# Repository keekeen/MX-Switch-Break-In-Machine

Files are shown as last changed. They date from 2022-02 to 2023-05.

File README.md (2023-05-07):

# MX Switch Break-In Machine
A simple machine designed to actuate/ break-in MX style switches consistently and repetitively for a smoother push feel. Watch the [assembly process and operation](https://www.youtube.com/watch?v=iYIlCdo38ZM&list=PLLd9RKaLkD3lO_kQBJ3w394Xko4Nm3RR9) of the machine here.

Also do check out my latest design and endeavour here: https://geekhack.org/index.php?topic=120229.msg3160750#msg3160750 🙆🏻‍♂️

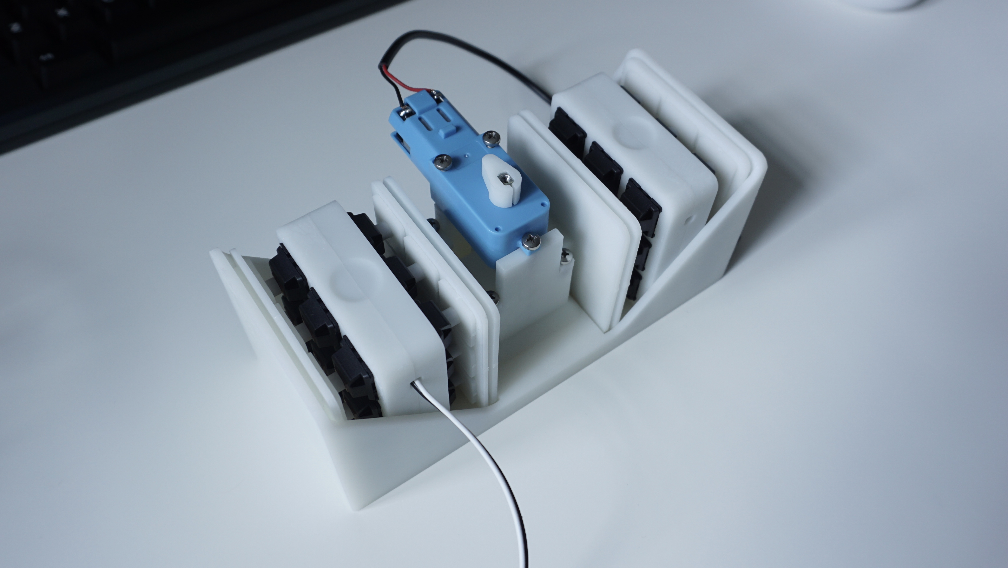
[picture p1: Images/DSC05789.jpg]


[snapshot]: /Images/DSC05789.jpg "Machine Snapshot"

## Specifications
- Max number of switches: 36
- Compatibility: 
  -  MX style switches with total travel distance of 4mm
  -  MX style switches with total travel distance less than 4mm (tweaks required for this)

## Notes ⚠️
- The provided files are to be used at your own risk.
- The dimensional tolerances may vary between 3D printers. See acceptable tolerances under [`Production/Technical-Drawings`](/Production/Technical-Drawings).
- The complete units showed in pictures and videos shared in this repo were printed with [JLCPCB 3D printing service](https://cart.jlcpcb.com/quote), with material of 8000 Resin, and remarked to print at an 30/45 angle for better Z-axis accuracy.
- Do ensure to run the machine at a ventilated area or fan-cooled to prevent the motor from overheating.

## Bill of materials (BOM) 📜
The following is the number of quantities required for each part to assemble a complete unit. The part files required to print are under the [`Production`](/Production) folder.

Parts required to print:
| Part | Qty | Comment |
| --- | --- | --- |
| Actuation Plate | 2 | - |
| Off Center Actuation Plate | 4 | - |
| Switch Holder | 4 | - |
| Flat Profile Keycap *or 10xFlat Profile Keycap* | 36 *or 4*  | - |
| Machine Housing | 1 | - |
| Machine Housing 1 *or 4xMachine Housing 1* | 2 *or 1* | - |
| Motor-Adjuster | 1 | - |
| Scotch Yoke | 1 | - |

Parts required to purchase:
| Part | Qty | Comment | References |
| --- | --- | --- | --- |
| TT 1:90 Gearbox DC Motor | 1 | Measured about 155 actutations/min, 5.4 hours for 50k actuations (measurement based on my purchased motor) | [link 1](https://shopee.sg/Large-Price-Metal-Gear-Robot-Smart-Car-Reduce-Speed-Motor-Tt-Motor-i.191993938.3917622642) |
| *or TT 1:48 Gearbox DC Motor* | 1 | Motor runs hot over long run, measured about 400 actutations/min, 2.1 hours for 50k actuations (measurement based on my purchased motor) | [link 2](https://www.adafruit.com/product/3777) |
| HK 0306 Needle Roller Bearing | 2 | - | [link 1](https://www.skf.com/us/products/rolling-bearings/roller-bearings/needle-roller-bearings/drawn-cup-needle-roller-bearings/productid-HK%200306%20TN) |
| M3 x 8mm Screw | 6 | - | - |
| M3 x 12mm Screw | 2 | - | - |
| M3 x 25mm Screw | 2 | - | - |
| Female USB C to 2-pin 22 AWG Wires | 1 | - | [link 1](https://www.aliexpress.com/item/1005001388133794.html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) <br> [link 2](https://www.aliexpress.com/item/1005002271810476.html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) |
| 8mm Diameter Bumpons | 4 | Optional | [link 1](https://shopee.sg/MAGIC-100PCS-Sheet-Soft-Buffer-Sticker-Furniture-Accessories-Gel-Shock-Absorber-Rubber-Silicone-Pads-Cabinets-Door-Stop-Anti-collision-Toilets-Bump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) |

## To-Do 📝
- A guide on breaking-in switches that have shorter travel distance will be shared soon.

## Changelog 📒
- `05/02/2022:` Initial part files commit 

## Reach me at 📩
- Discord: https://discordapp.com/users/keekeen#1351
  - Feel free to send me your enquires if you have doubt reproducing a unit for yourself.

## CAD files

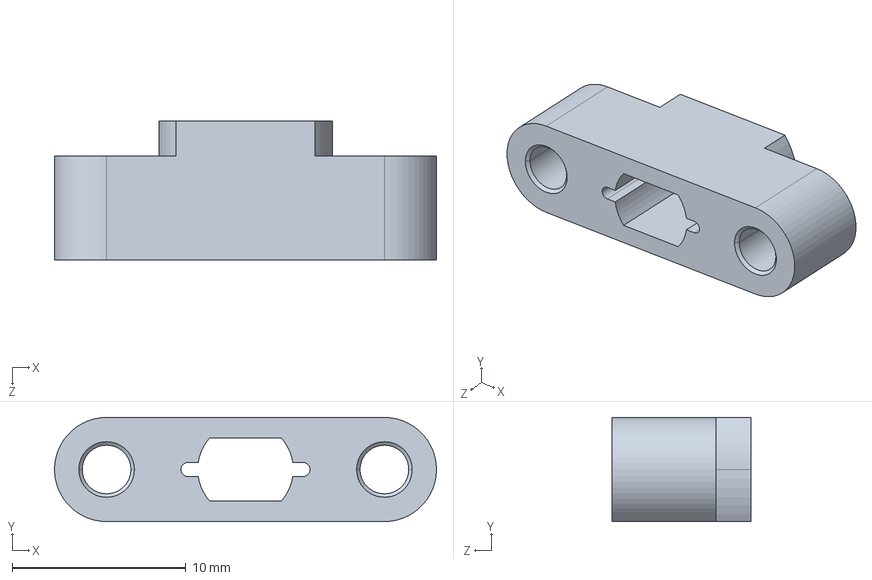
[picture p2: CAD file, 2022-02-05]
Production/STEP/Scotch-Yoke.STEP
22.0 x 6.00 x 8.00 mm

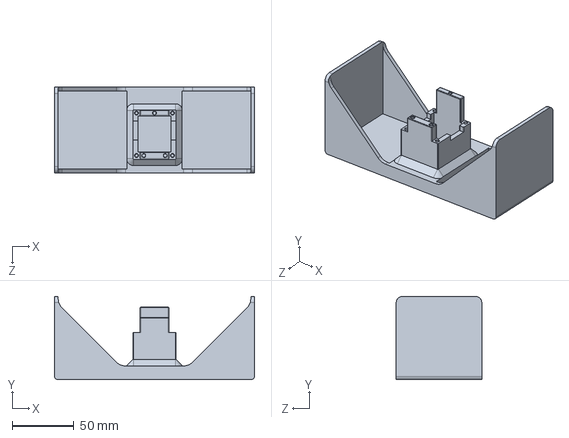
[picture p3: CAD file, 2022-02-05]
Production/STEP/Machine-Housing.STEP
161.3 x 67.0 x 69.0 mm

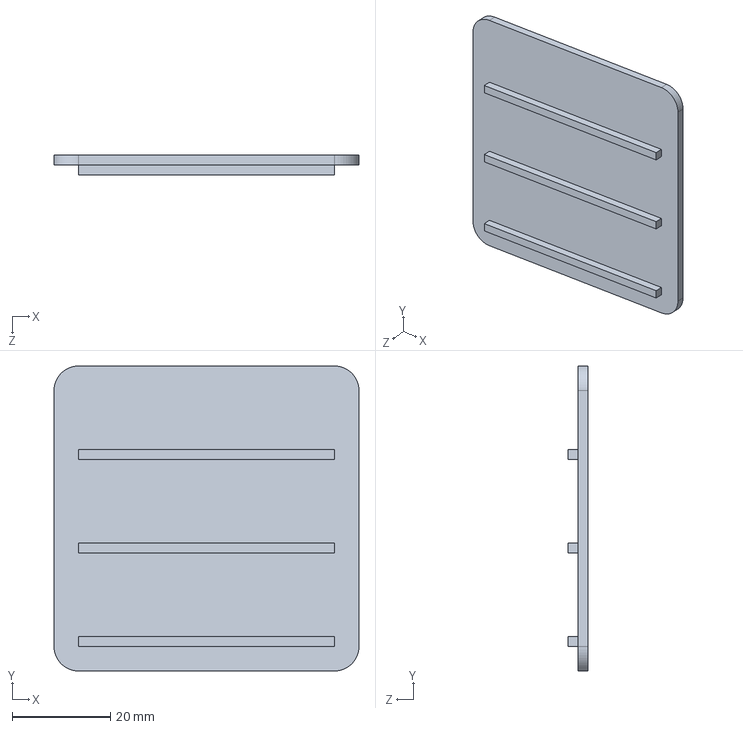
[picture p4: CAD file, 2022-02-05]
Production/STEP/Off-Center-Plate.STEP
62.0 x 62.0 x 4.00 mm

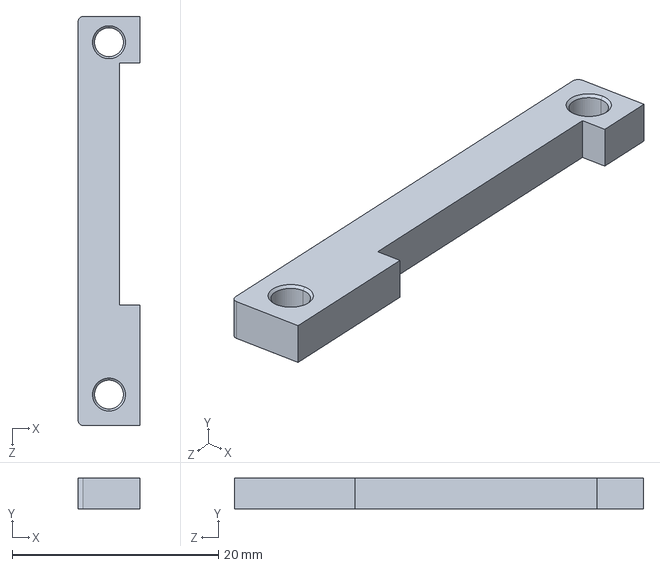
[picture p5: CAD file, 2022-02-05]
Production/STEP/Machine-Housing-1.STEP
6.00 x 3.00 x 39.7 mm

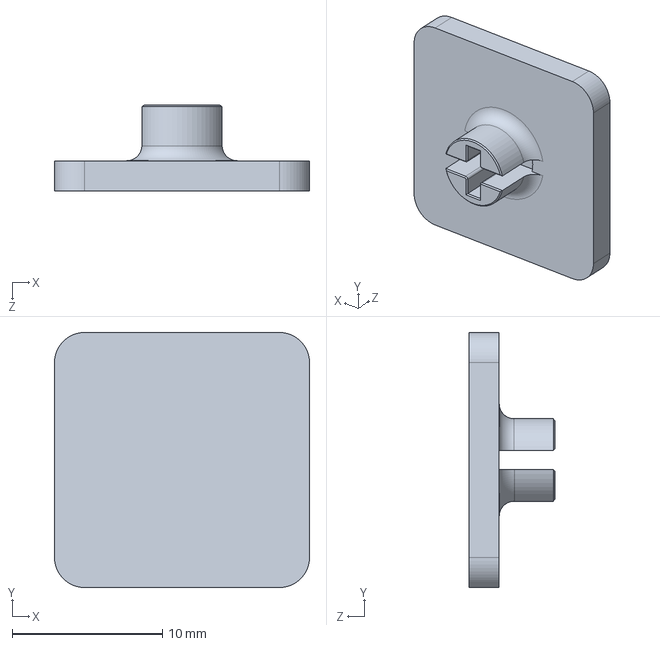
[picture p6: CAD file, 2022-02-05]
Production/STEP/Flat-Profile-Keycap.STEP
17.0 x 17.0 x 5.70 mm

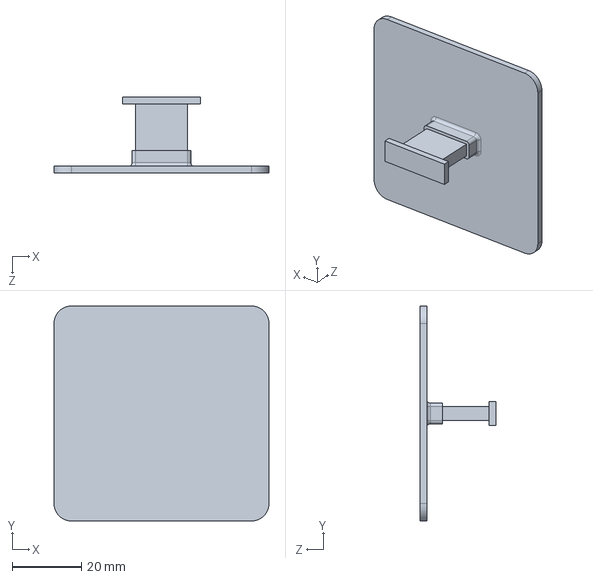
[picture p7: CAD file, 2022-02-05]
Production/STEP/Actuation-Plate.STEP
62.0 x 62.0 x 22.0 mm

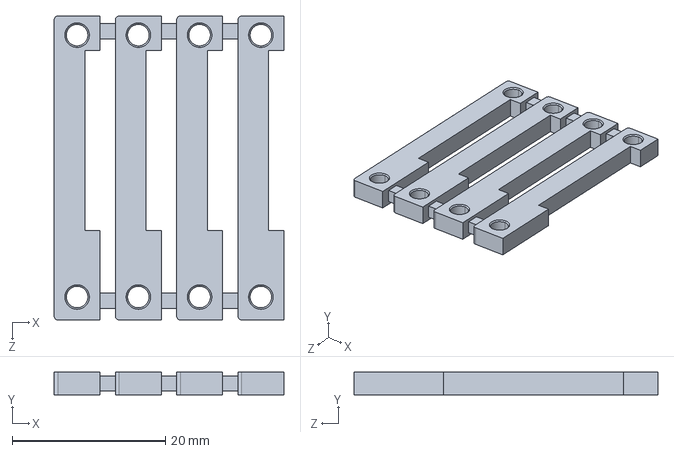
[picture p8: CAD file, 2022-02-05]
Production/STEP/4xMachine-Housing-1.STEP
30.0 x 3.00 x 39.7 mm

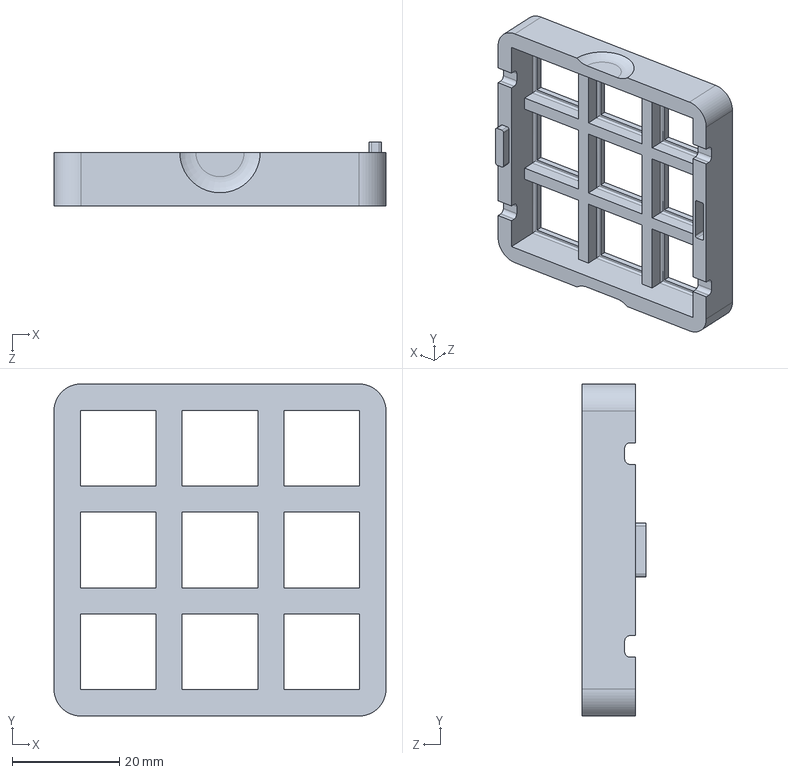
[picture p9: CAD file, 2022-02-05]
Production/STEP/Switch-Holder.STEP
62.0 x 62.0 x 12.0 mm

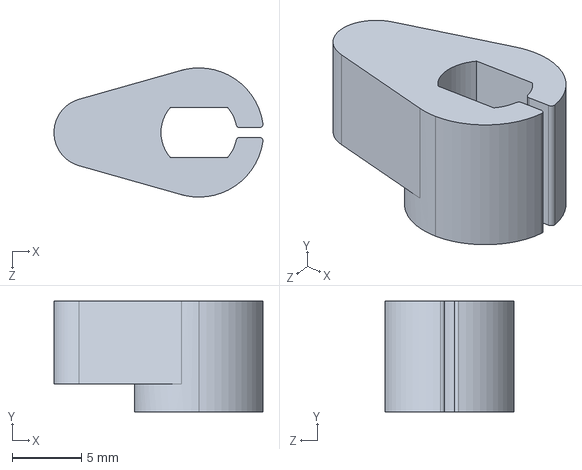
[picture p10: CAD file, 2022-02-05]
Production/STEP/Motor-Adjuster.STEP
15.1 x 8.00 x 9.35 mm

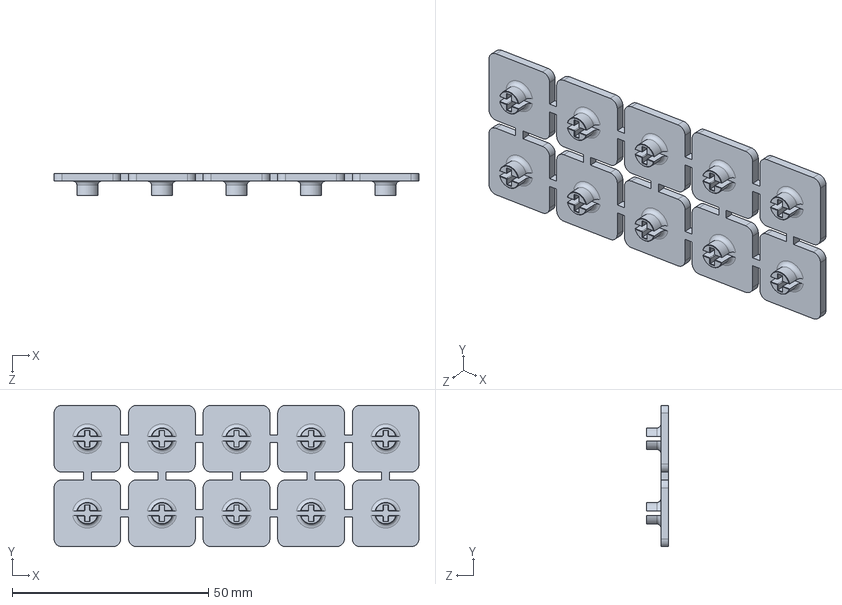
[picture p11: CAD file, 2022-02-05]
Production/STEP/10xFlat-Profile-Keycap.STEP
93.0 x 36.0 x 5.70 mm

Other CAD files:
Production/STL/10xFlat-Profile-Keycap.STL
Production/STL/4xMachine-Housing-1.STL
Production/STL/Actuation-Plate.STL
Production/STL/Flat-Profile-Keycap.STL
Production/STL/Machine-Housing-1.STL
Production/STL/Machine-Housing.STL
Production/STL/Motor-Adjuster.STL
Production/STL/Off-Center-Plate.STL
Production/STL/Scotch-Yoke.STL
Production/STL/Switch-Holder.STL

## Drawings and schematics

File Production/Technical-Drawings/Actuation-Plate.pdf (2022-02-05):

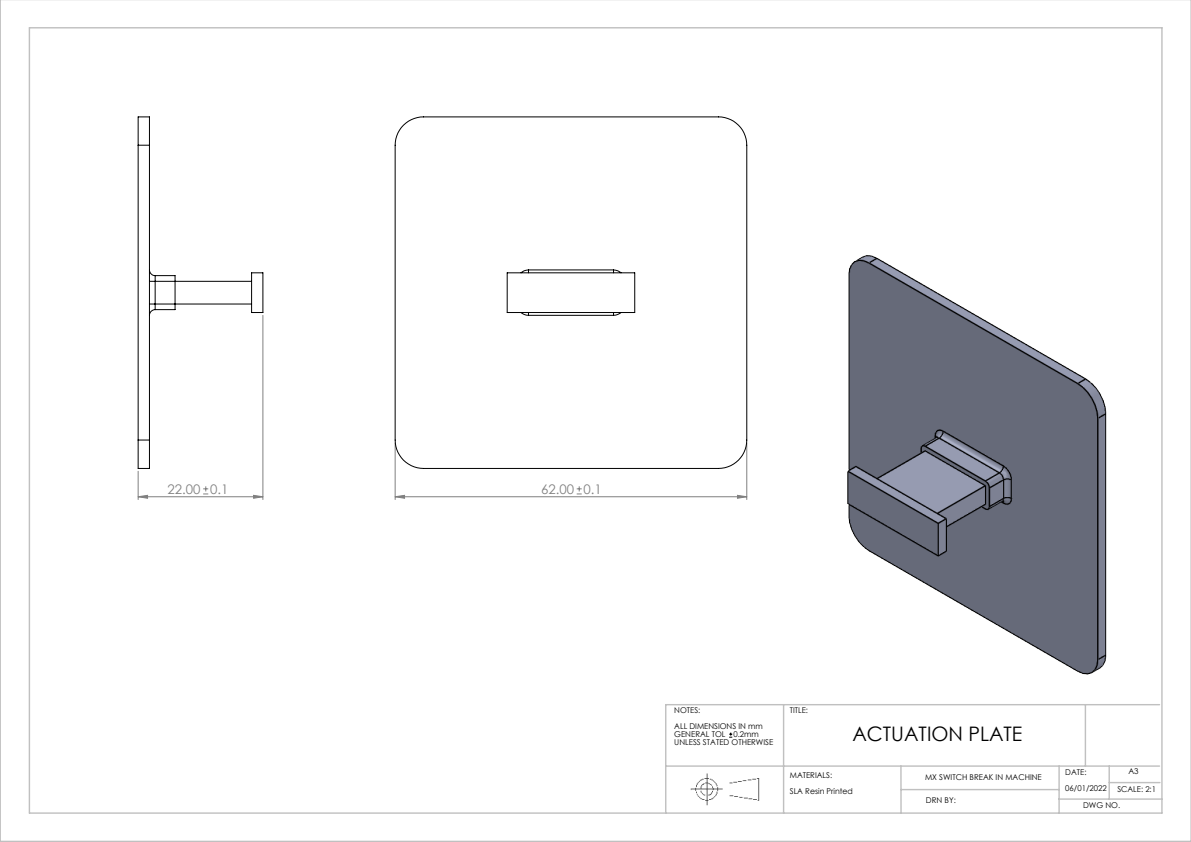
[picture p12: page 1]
DWG NO.; SCALE: 2:1; DRN BY:

NOTES: ALL DIMENSIONS IN mm GENERAL TOL 0.2mm UNLESS STATED OTHERWISE | TITLE: ACTUATION PLATE

MATERIALS: SLA Resin Printed | MX SWITCH BREAK IN MACHINE | DATE: 06/01/2022 | A3

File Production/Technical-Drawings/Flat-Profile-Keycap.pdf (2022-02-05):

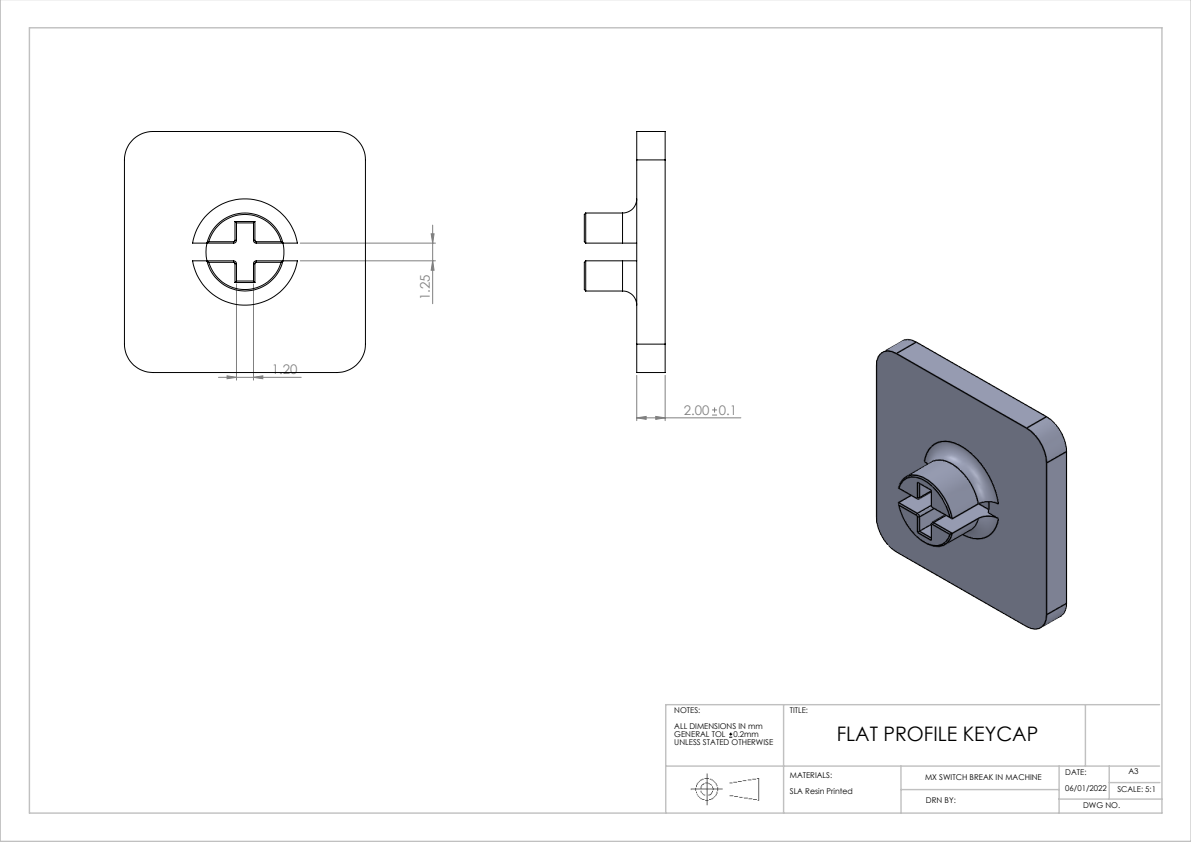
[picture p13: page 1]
DWG NO.; SCALE: 5:1; DRN BY:

NOTES: ALL DIMENSIONS IN mm GENERAL TOL 0.2mm UNLESS STATED OTHERWISE | TITLE: FLAT PROFILE KEYCAP

MATERIALS: SLA Resin Printed | MX SWITCH BREAK IN MACHINE | DATE: 06/01/2022 | A3

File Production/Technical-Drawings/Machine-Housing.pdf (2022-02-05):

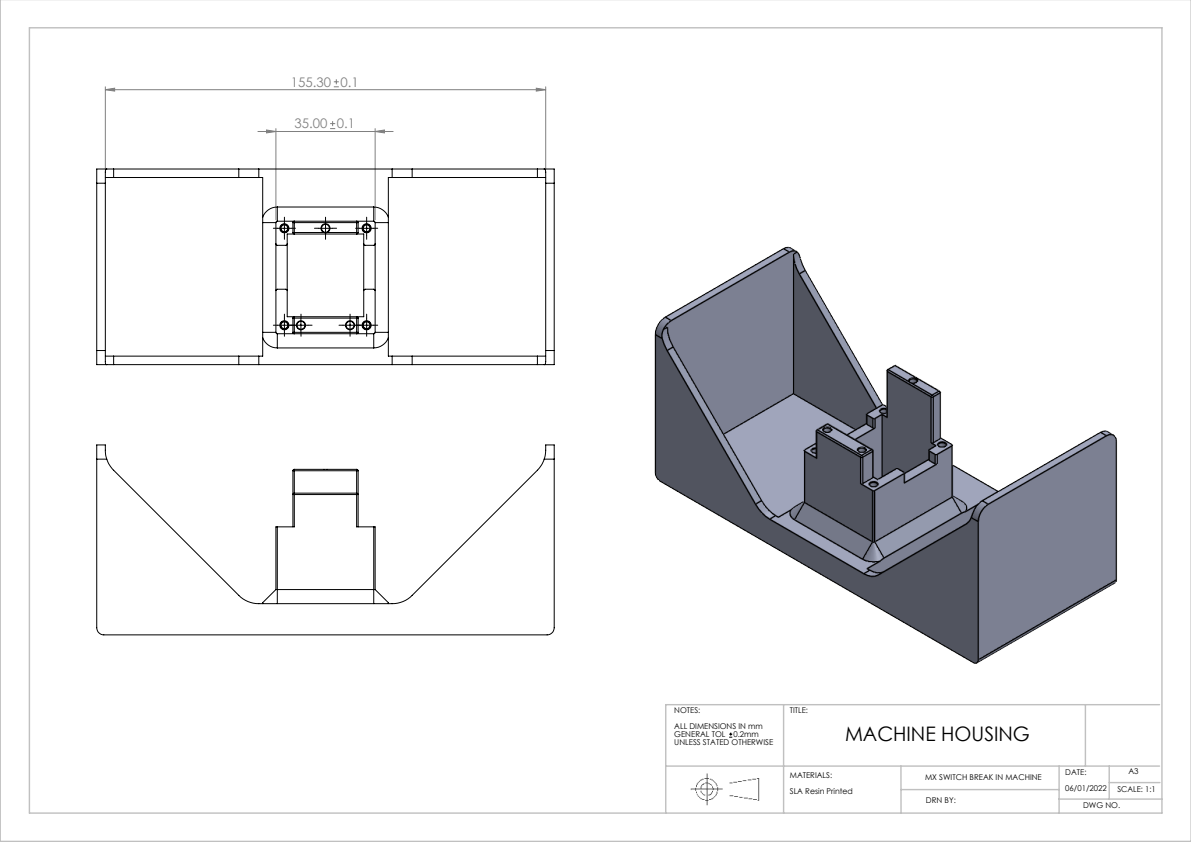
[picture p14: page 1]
DWG NO.; SCALE: 1:1; DRN BY:

NOTES: ALL DIMENSIONS IN mm GENERAL TOL 0.2mm UNLESS STATED OTHERWISE | TITLE: MACHINE HOUSING

MATERIALS: SLA Resin Printed | MX SWITCH BREAK IN MACHINE | DATE: 06/01/2022 | A3

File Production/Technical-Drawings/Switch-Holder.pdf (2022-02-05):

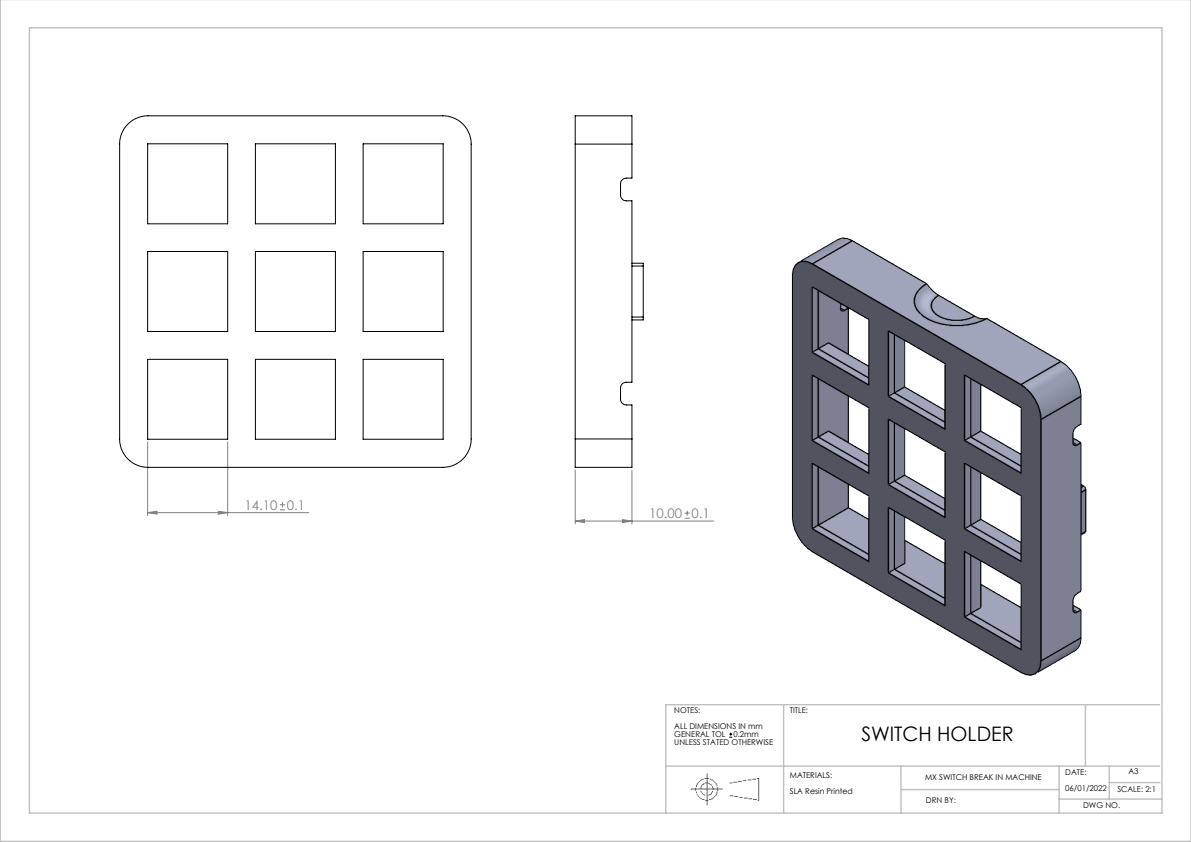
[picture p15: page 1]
DWG NO.; SCALE: 2:1; DRN BY:

NOTES: ALL DIMENSIONS IN mm GENERAL TOL 0.2mm UNLESS STATED OTHERWISE | TITLE: SWITCH HOLDER

MATERIALS: SLA Resin Printed | MX SWITCH BREAK IN MACHINE | DATE: 06/01/2022 | A3
